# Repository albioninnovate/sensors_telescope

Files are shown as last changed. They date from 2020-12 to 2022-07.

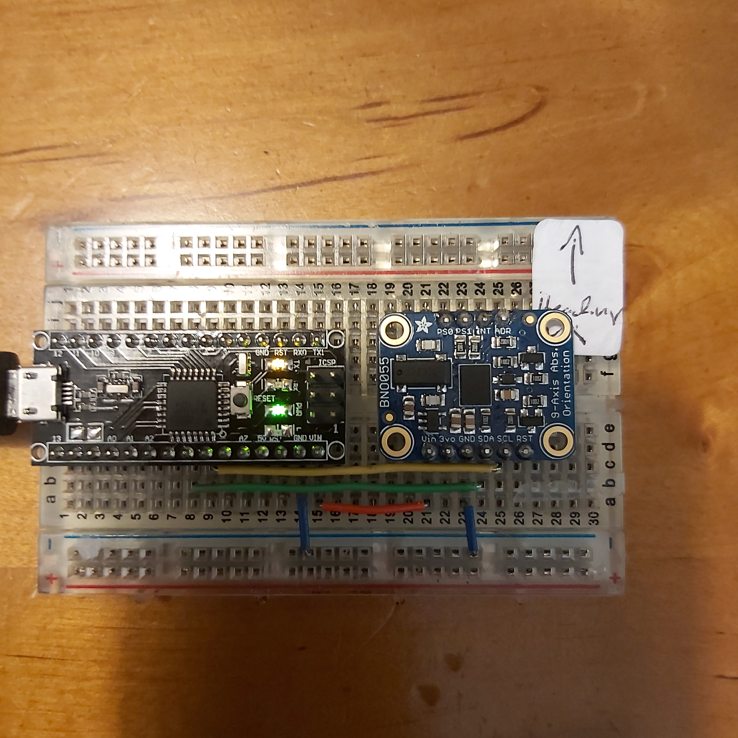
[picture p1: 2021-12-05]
arduino/images/20201223_222857.jpg

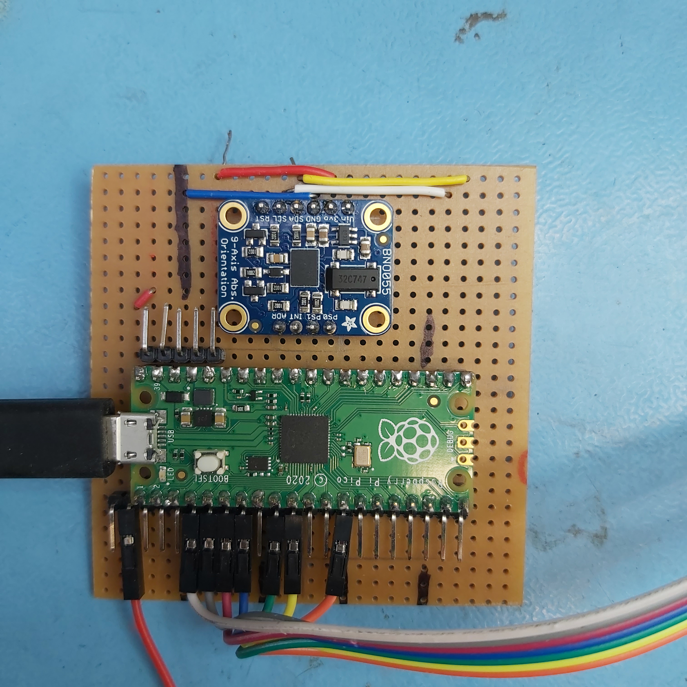
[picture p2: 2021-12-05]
Images/20210328_164021.jpg

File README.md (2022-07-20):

# Sensors_telescope
Sensor package for positioning telescope, to track targets, interfacing with astronomy software (Stellarium). 

## BNO055 Board layout and orientation:
         +----------+
         |         *| RST   PITCH  ROLL  HEADING
     ADR |*        *| SCL
     INT |*        *| SDA     ^            /->
     PS1 |*        *| GND     |            |
     PS0 |*        *| 3VO     Y    Z-->    \-X
         |         *| VIN
         +----------+

# Design

## Hardware configuration choice 

The initial strategy was to connect the BNO055 to a Raspberry Pi via I2C.  Although it was easy enough to get data from the sensor package the values were erratic.  Several approaches were taken too, speed up data collection, take larger samples followed by averaging and also to carry the data in quaternions and calculate the Euler angels in the last step. It seems the I2C connection is perhaps not fast enough to collect the useful measurements.

A second strategy it was much more successful. This was using an I2C connection via an Arduino and a USB connection between the Arduino and a Raspberry Pi.  The data return was very steady.   The demo Arduino scripts were more than sufficient to return the heading, pitch and yaw (azimuth, altitude and tilt) along with some data quality indicators. 

## Data choice 
The BNO055 outputs several types of direct measurements (Mag, Gyro, Acc, etc) and two sets of derived information, Euler Angles and Quaternions.  A quick review of literature suggests that Euler Angles can be problematic, and it is best to use quaternions in any data manipulations only converting to Euler angels in the last steps. 
This does not see to hold for the BNO055.  Initially data was erratic prompting a strategy of averaging the output.  The output is received in multi layer dictionary structures, so a utility was written to flatten the dictionary and average them (utils/flatten_dict.py).  Another utility was written to convert quaternions to Euler angels (utils/quaternion.py). 

The Euler angles output it from the sensor seem to be quite stable and correspond well with the orientation of the chip.  the decision was made to use the output from the chip directly ignoring the quaternions for now. It is worth investigating the processing done on the microprocessor of the BNO055 there appears to be some smoothing in the output data evidenced by its stability. 

When the Euler angles are sent Stellarium they must first be inverted by multiplying by -1 and then converting into radians 

## Python Choice 

Python => 3.8 is used in order to access asyncio functions.

An installation was created here:
```
/home/pi/Python-3.8.5
```

There are two installations of Python on this Raspberry Pi 3.5 is the standard which can be accessed by  $ python <>.py.  There is also an installation of Python 3.8 (home/pi/Python-3.8.5 which can be accessed with python38. <>.py.  The alias of this second installation is controlled in bashrc.
```
sudo nano /home/pi/.bashrc
```

the following line was added at the end of the file: 
```
alias python38="/home/pi/Python-3.8.5/python"
```

The reason for doing this was to access functionality in the asyncio package, specifically the. run method of that package. Running under early versions of python causes this error: 

AttributeError: module 'asyncio' has no attribute 'run'

### Installing packages 
Installing packages to this alternative python can be done via pip specifying  python38.
```
python38 -m pip install adafruit-circuitpython-bno055
```

## Information flow

It is anticipated that the information produced by the sensor will be used for more than one application for example; direct display at the telescope, feedback to the positioning system and sending orientation information to external programmes like Stellarium.  To accommodate this an architecture which allowed the sensor to continually produce data that could be requested by various clients.  

The system comprises a BNO055 connected by I2C to an Arduino sending data via a serial connexion to a Raspberry Pi running a simple server which is available over an IP network.   



# Telescope Capabilities

The goal of the project is that the pointing direction of the Optical Tube Assembly (OTA) is available to the user with only 5v power at the telescope. The user should be able to have "push to" functionally without any other computer or network connection.  This implies that simple calibrations are part of the system.   This latter capability is only practically possible with a some type of use interface, say buttons on the LCD screen.  

If more computing capability, and power is available, data recording, coordination with astronomy software (e.g. Stellarium), or motor drivers become a goal. 

# Ardunio setup 

ref: https://learn.adafruit.com/adafruit-bno055-absolute-orientation-sensor/arduino-code

an Arduino Mega was used for prototyping and in the future is a possibility for driving motors.  To connect the assembled BNO055 breakout to an Arduino

Pinouts:

| BNO055 | Arduino Mega | Arduino Nano |
| :--- | :---: | ---: |
|  SCL | 21  | A5 |
| SDA  | 20 | A4 |
| VIN  | 5v | VIN |
| GND  | GND | GND |

for mounting on the telescope the smaller form factor of a nano has advantages. 

See the Adafruit instructions for the necessary libraries.  The sketch is here arduino/bno055/bno055.ino.  Note the directory 'bno055' is needed by the Arduino IDE, do not remove it.

# PICO set up 

## Pinouts

## Software

### Circuitpython

#### Installation 

#### Requirements

#### Software
 bno055.py

 lcd_rgb.py

# LCD Screen

Adafruit RGB Negative 16x2 LCD+Keypad Kit for Raspberry Pi (ref: https://www.adafruit.com/product/1110

* pull up resistors needed, 5v logic 

Character LCD
https://circuitpython.readthedocs.io/projects/charlcd/en/latest/

# Server

In development and testing a Rpi 3 running a fresh installation of Buster was used.

Running the server has several requirements.

* Start on boot so that all that is required in the field is power on. 
* Be accessible via fixed IP or hostname from the laptop
* the host name needs to match in both the server and the client.  The host name should match the server, e.g. triscopepi.local or devpi.local.
* TODO add the host name to the configuration file so thi can be changed in just one place.
``` 
triscopepi.local
```
* Robustly find the serial port of the PICO/Arduino 

## Start on boot

Crontab is used to launch the server when the Rpi is powered. An updated version of Python3 was added to gain asyncio (https://docs.python.org/3.7/library/asyncio.html). 

ref: https://www.raspberrypi.org/documentation/linux/usage/cron.md

Edit Crontab on the Rpi by opening a terminal and executing the command: 
```
crontab -e
```

If asked select the nano editor.  In the file that opens, add this line.
```
@reboot sleep 30;/usr/bin/python3 /home/pi/code/sensors_triscope/rpi/server.py
```
A python version later than 3.7 be used so that asyncio is available.  A sleep of 30 seconds allows the Rpi to fully boot and establish network connections.  This has not be fully tested so other values, or elimination,  might also work

the sleep 30, allow time for the network connection and IP address to be established.  

There is an alternative approach for launching the server at startup, Systemd.  NOTE, the following approach has not always 
worked, while the cron approach has been reliable. 

---
see: 
    rpi/README_server.md
---
Setting server to run on RaspberryPi boot:
    
Create a Unit file 
```
sudo nano /lib/systemd/system/triscope_server.service
````

Add this text 
```
 [Unit]
 Description= Sensors Triscope Server
 After=multi-user.target

 [Service]
 Type=idle
 ExecStart=/usr/bin/python3 /home/pi/code/sensors_triscope/rpi/server.py

 [Install]
 WantedBy=multi-user.target
```

Set permission of the unit file to: 

```
sudo chmod 644 /lib/systemd/system/triscope_server.service
```

----

# client 
in the line:
  reader, writer = await asyncio.open_connection('triscopepi.local', 8888)

the host name can be used if that matches the IP address. In the case of two networks being active (Ethernet and WI-FI) the Rpi may have two addresses.  The connection can be forced over the direct link ether net byt switching off the WI-FI and making a call to the server via the host name.  After this is done the Wi-Fi can be switched back on with the host name remaining associated  with the ethernet connection   

# Stellarium Set up

ref https://stellarium.org/doc/head/remoteControlApi.html

Launch Stellarium Application 

Go to 	
1. Configuration Menu (F2)
2. Select the Plug-ins icon (top of dialogue box)
3. Select Remote Control plug-in (left of dialogue box)
4. Check box - launch at startup

Restart Stellarium Application to load plug-in

Return to the Remote Control plug-in

1. Click the Configure button
2. Check box: the Server enabled box 
   1. Returns: listening on 127.0.1.1
3. Confirm: Port number: 8096
4. Check box: Enable automatically at start up 
5. Save settings

# Real Time Clock 
ref: https://learn.adafruit.com/adafruit-pcf8523-real-time-clock/rtc-with-circuitpython

to run on PICO 

requirements: 

    adafruit_bus_device folder
    adafruit_register folder
    adafruit_pcf8523.mpy

to Set the time: 
``` 
if False:   # change to True if you want to write the time!
    #                     year, mon, date, hour, min, sec, wday, yday, isdst
    t = time.struct_time((2017,  10,   29,   15,  14,  15,    0,   -1,    -1))
    # you must set year, mon, date, hour, min, sec and weekday
    # yearday is not supported, isdst can be set but we don't do anything with it at this time

```

Change the False to True in the first line, and update the time.struct_time to have the current time starting from year to weekday. The last two entries can stay at -1

Note the part where the program says it is Setting time to:

Now you can go back and change the if True to if False and save, so you don't re-set the RTC again.

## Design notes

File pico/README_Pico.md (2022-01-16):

## PICO set up

The directory PICO_requirements contains all the files and lib requirements 
needed to run bno055.py and bno055_display.  Place it in the 
PICO directory ' CIRCUITPY '.   USe Mu to run and serial to display the 
output

# CircuitPython 

latest drivers can be found here:
https://github.com/adafruit/Adafruit_CircuitPython_Bundle/releases

https://github.com/adafruit/Adafruit_CircuitPython_Bundle/releases/tag/20220114

TODO  copy the active code and requirements folder from the PICO on the Triscope 

To reset PICO:
https://www.raspberrypi.com/documentation/microcontrollers/raspberry-pi-pico.html#resetting-flash-memory
https://datasheets.raspberrypi.com/soft/flash_nuke.uf2

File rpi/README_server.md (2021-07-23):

# Server

## Architecture choice 

TODO

## Supporting modules 

### ard_ser.py

TODO

## Sever set up

There are two approaches to launching the server at boot; systemd and crontab.

### crontab

```
crontab -e
```

Place the following text at the bottom of the file

```
@reboot sleep 30;/usr/bin/python3 /home/pi/code/sensors_triscope/rpi/server.py
```

----

### systemd

ref https://www.raspberrypi-spy.co.uk/2015/10/how-to-autorun-a-python-script-on-boot-using-systemd/

The intention is that the server.py module runs at boot of the RaspberryPi platform. This allows reset of the Raspberrypi-Arduino-BNO055 system to be reset with a power cycle of the Raspberrypi. The Arduino and sensor are powered by the Raspberrypi via the USB port.  

The server is at this location in the repository to allow ready maintenance: 
```
home/pi/code/sensors_telescope/raspberrypi/server.py
```

systemd is used to manage the startup process.  Systems is configured in a 'unit file'

``` 
 sudo nano /lib/systemd/system/server.service
 ```

this project uses the python3.7+ in order to access the asyncio features (TODO add reference to main README.md)

Add in the following text :
```
[Unit]
 Description=Sensors_telescope_server
 After=multi-user.target

 [Service]
 Type=idle
 ExecStart=/home/pi/Python-3.8.5/python /home/pi/code/sensors_triscope/rpi/server.py > /home/pi/code/sensors_triscope/rpi/server.log 2>&1

 [Install]
 WantedBy=multi-user.target
```

In order to store the script’s text output in a log file you can change the ExecStart line to :
```
ExecStart=/home/pi/Python-3.8.5/python home/pi/code/sensors_telescope/rpi/server.py > home/pi/code/sensors_telescope/rpi/server.log 2>&1

```

The permission on the unit file needs to be set to 644 :
```
sudo chmod 644 /lib/systemd/system/server.service
```

Configure systemd

Now the unit file has been defined we can tell systemd to start it during the boot sequence :

``` 
 sudo systemctl daemon-reload
 sudo systemctl enable server.service
 ```

Reboot the Pi and your custom service should run :

sudo reboot

The status of the server can be checked with:
 ```
 sudo systemctl status server.service
 
 sudo systemctl status /home/pi/Python-3.8.5/python home/pi/code/sensors_telescope/rpi/server.py 
 ```

### Troubleshooting 

sudo -H pip3 install serial -t /home/pi/Python-3.8.5

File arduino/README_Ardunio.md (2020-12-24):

ref: https://learn.adafruit.com/adafruit-bno055-absolute-orientation-sensor/arduino-code

## From AdaFruit
To connect the assembled BNO055 breakout to an Arduino Uno, follow the wiring diagram.

    Connect Vin (red wire) to the power supply, 3-5V is fine. Use the same voltage that the microcontroller logic is based off of. For most Arduinos, that is 5V
    Connect GND (black wire) to common power/data ground
    Connect the SCL (yellow wire) pin to the I2C clock SCL pin on your Arduino. On an UNO & '328 based Arduino, this is also known as A5, on a Mega it is also known as digital 21 and on a Leonardo/Micro, digital 3
    Connect the SDA (blue wire) pin to the I2C data SDA pin on your Arduino. On an UNO & '328 based Arduino, this is also known as A4, on a Mega it is also known as digital 20 and on a Leonardo/Micro, digital 2

## Arduino Nano
SCL - A5
SDA - A4
VIN - VIN
GND - GND

## Board layout:
         +----------+
         |         *| RST   PITCH  ROLL  HEADING
     ADR |*        *| SCL
     INT |*        *| SDA     ^            /->
     PS1 |*        *| GND     |            |
     PS0 |*        *| 3VO     Y    Z-->    \-X
         |         *| VIN
         +----------+

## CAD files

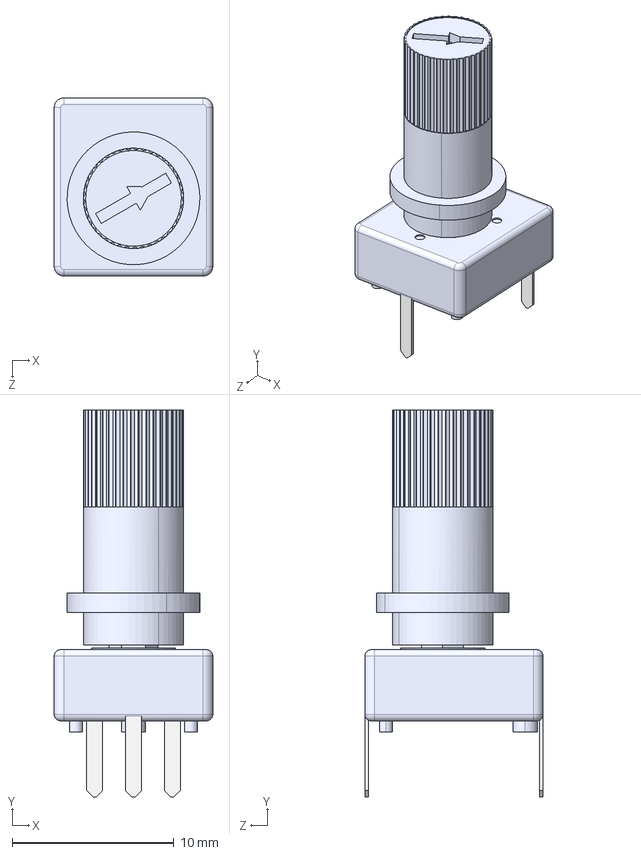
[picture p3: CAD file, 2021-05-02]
3d_model/Potentiometer_Square/PotSquareAssySTEP.STEP
9.80 x 23.9 x 11.0 mm
Pot_SquareBase
ShaftSocket
ShaftKnob

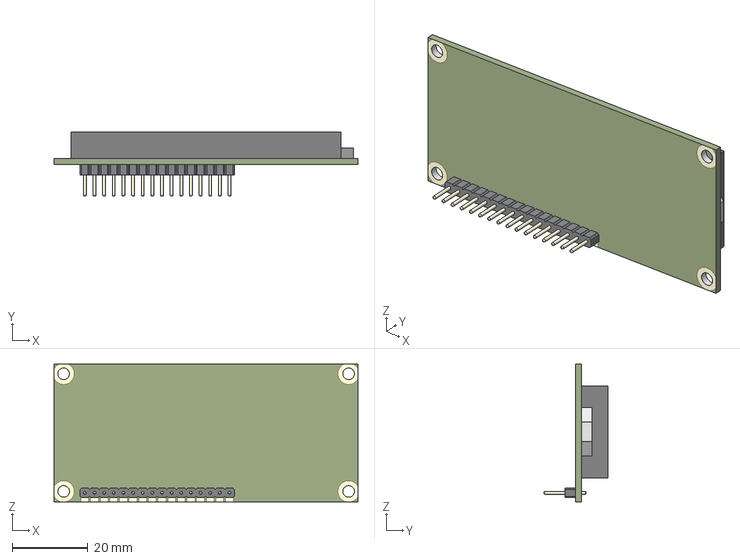
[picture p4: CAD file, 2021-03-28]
3d_model/1602a-lcd-module-1.snapshot.1/1602A - LCD w Header Pins.stp
80.1 x 17.0 x 36.3 mm
1602A - 16x2 LCD
16pin, Single Row, Male, Header, 0.1in pitch

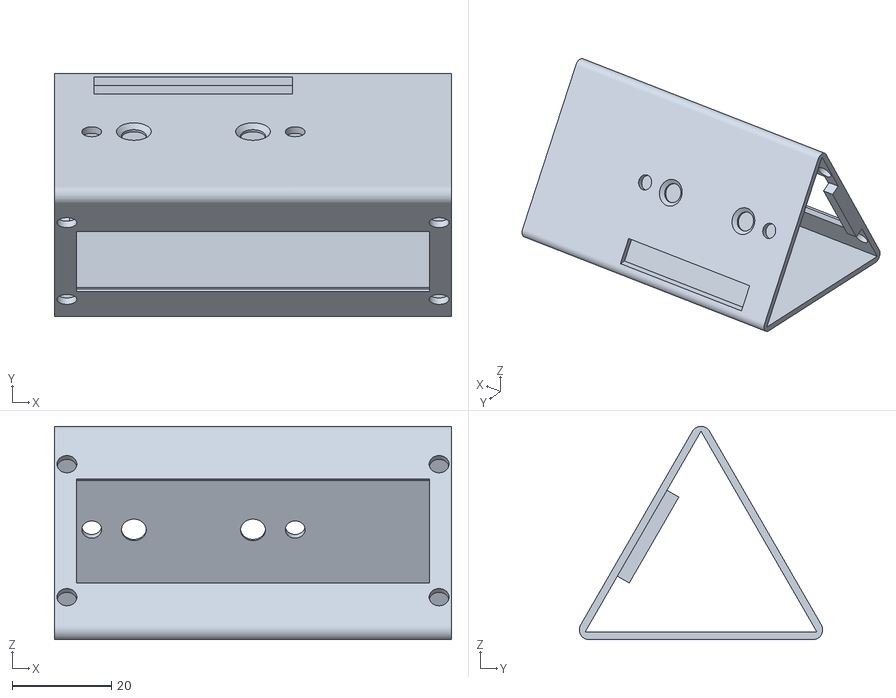
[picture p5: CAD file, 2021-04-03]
3d_model/LCD_case/LCD_case-Fusion007.stl
80.0 x 49.0 x 43.0

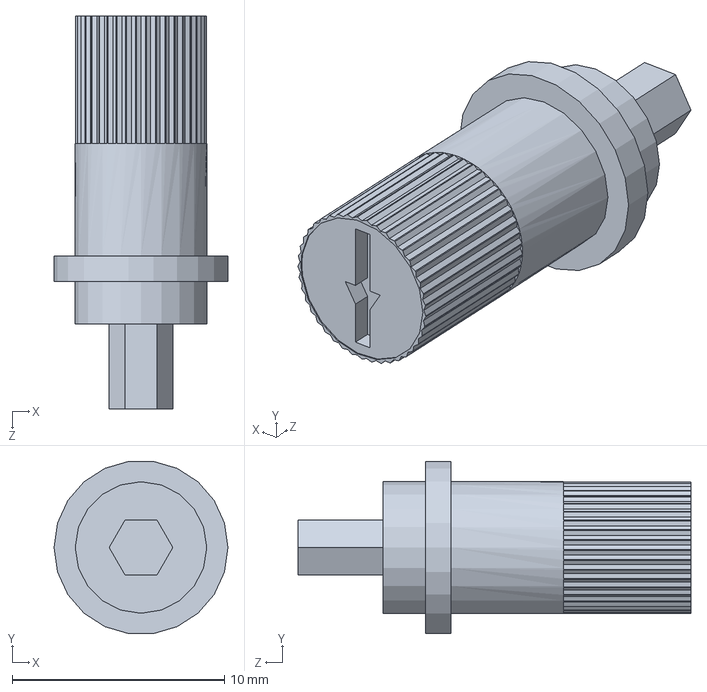
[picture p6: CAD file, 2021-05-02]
3d_model/Potentiometer_Square/ShaftKnob.SLDPRT
8.20 x 8.12 x 18.5 mm

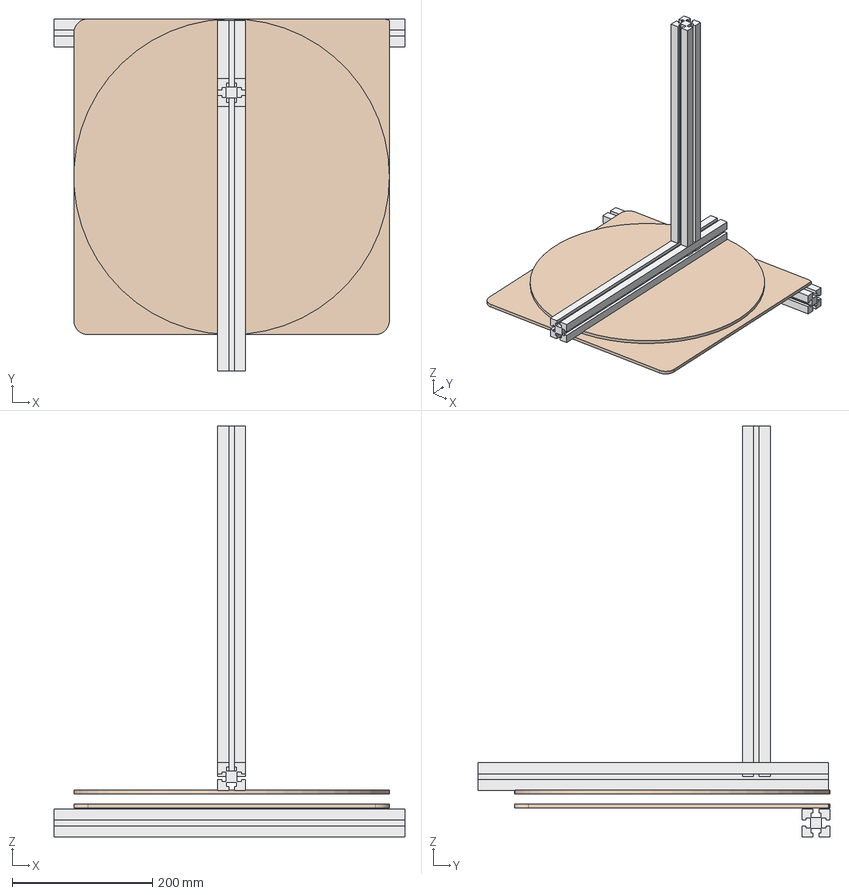
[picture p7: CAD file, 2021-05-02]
3d_model/Stand.FCStd
500.0 x 502.0 x 586.0 mm
Stand_Base
Stand_Strut
Stand_Strut_Base_001
Stand_Strut_Cross

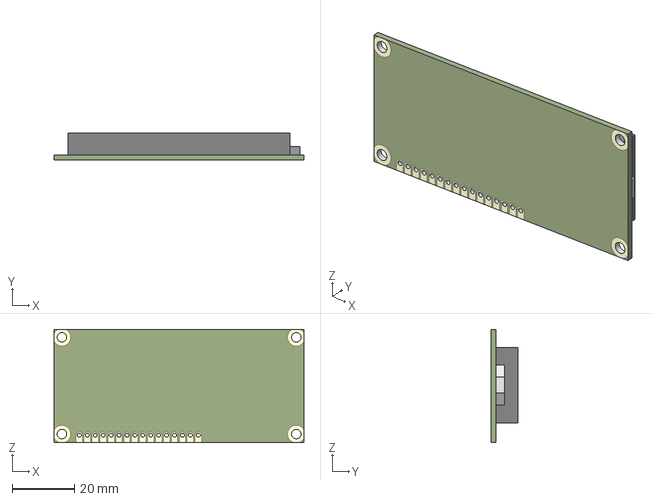
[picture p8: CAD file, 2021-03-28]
3d_model/1602a-lcd-module-1.snapshot.1/1602A - 16x2 LCD.stp
80.1 x 8.59 x 36.3 mm

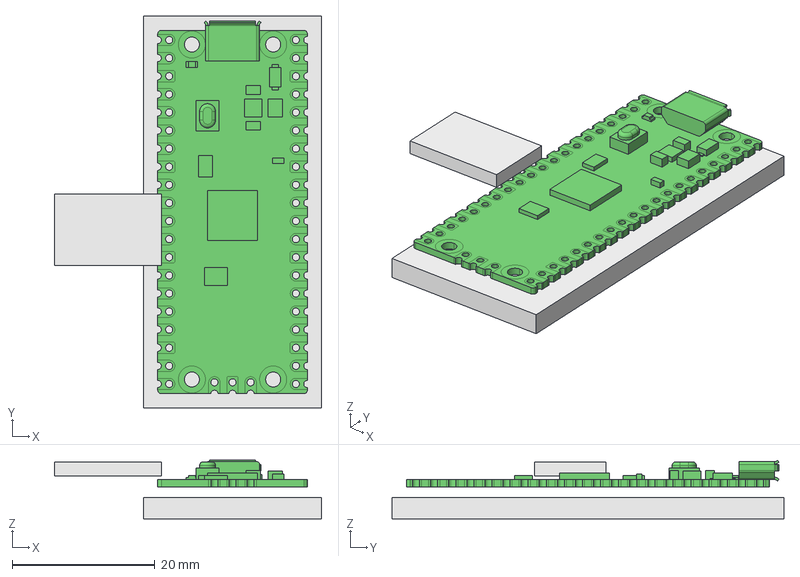
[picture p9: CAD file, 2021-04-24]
3d_model/pico-mount.FCStd
37.5 x 55.0 x 8.23 mm
pico-mount
PICO001

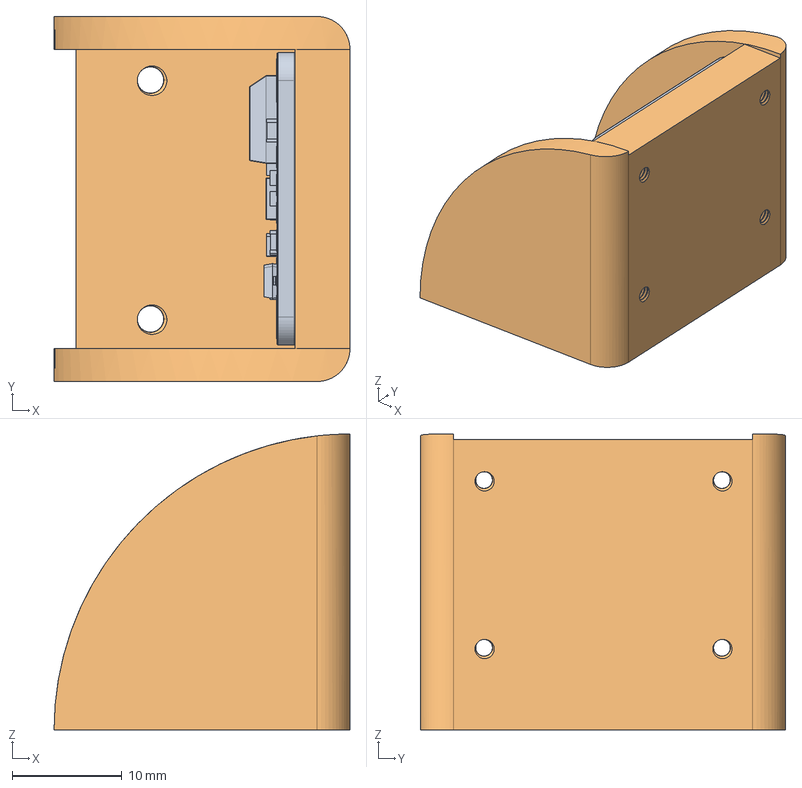
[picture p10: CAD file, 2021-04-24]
3d_model/bno055_mount.FCStd
27.0 x 33.3 x 27.0 mm
Adafruit_BNO055_AP214
BNO055-mount
BNO055-mount001

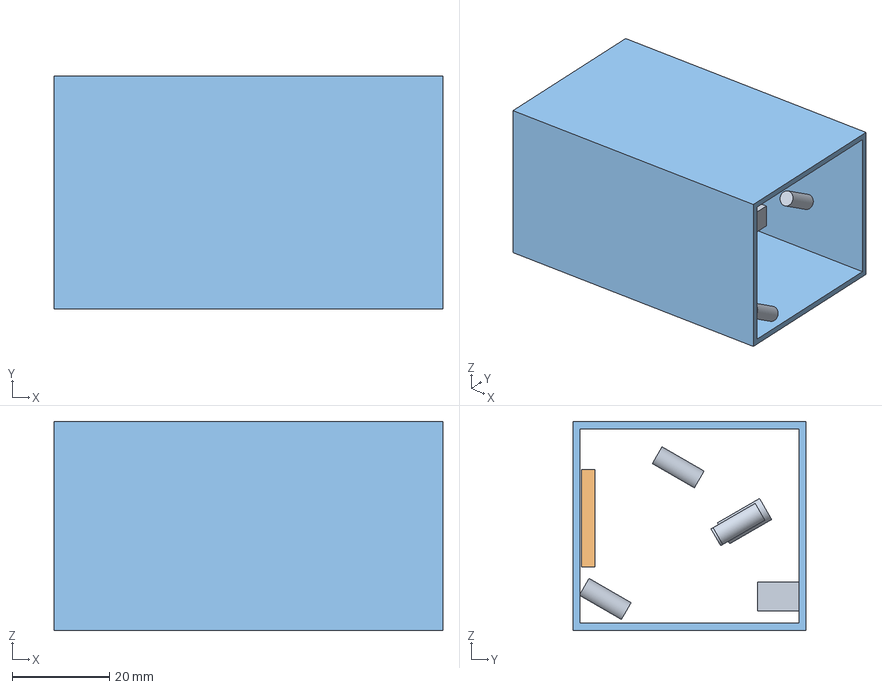
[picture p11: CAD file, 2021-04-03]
3d_model/LCD_case_sqr.FCStd
80.0 x 48.0 x 43.0 mm
LCD_case_tools
lcd_rest
Case

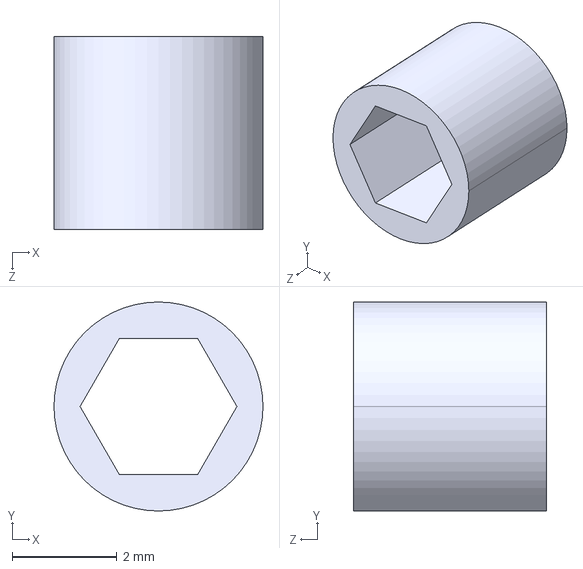
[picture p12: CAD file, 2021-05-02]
3d_model/Potentiometer_Square/ShaftSocketSTEP.STEP
4.00 x 4.00 x 3.70 mm

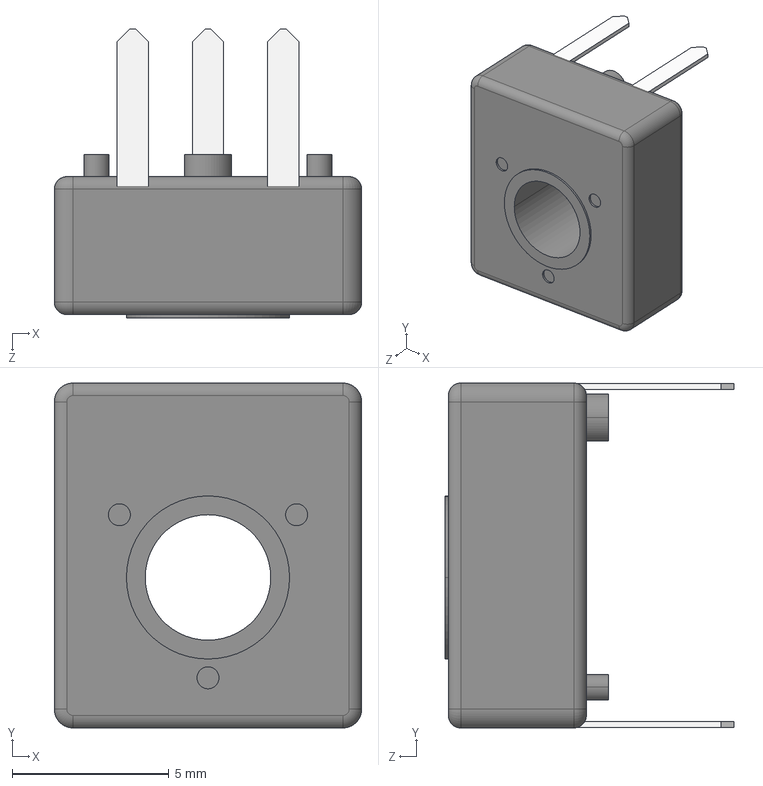
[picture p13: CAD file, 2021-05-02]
3d_model/Potentiometer_Square/Pot_SquareBaseSTEP.STEP
9.80 x 11.0 x 9.20 mm

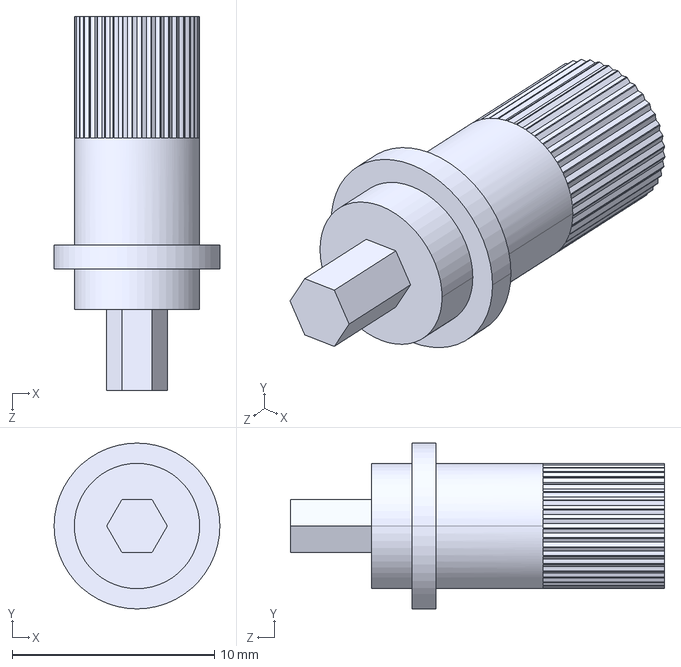
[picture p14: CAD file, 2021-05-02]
3d_model/Potentiometer_Square/ShaftKnobSTEP.STEP
8.20 x 8.20 x 18.5 mm

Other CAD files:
3d_model/Potentiometer_Square/PotSquareAssy.SLDASM
3d_model/LCD_case.FCStd
3d_model/Potentiometer_Square/ShaftSocket.SLDPRT
3d_model/Potentiometer_Square/Pot_SquareBase.SLDPRT

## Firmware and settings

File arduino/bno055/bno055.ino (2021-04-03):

#include <Wire.h>
#include <Adafruit_Sensor.h>
#include <Adafruit_BNO055.h>
#include <utility/imumaths.h>

/* This driver reads raw data from the BNO055

   Connections
   ===========
   Connect SCL to analog 5
   Connect SDA to analog 4
   Connect VDD to 3.3V DC
   Connect GROUND to common ground

   History
   =======
   2015/MAR/03  - First release (KTOWN)
*/

/* Set the delay between fresh samples */
/* #define BNO055_SAMPLERATE_DELAY_MS (100) */
#define BNO055_SAMPLERATE_DELAY_MS (1000)

// Check I2C device address and correct line below (by default address is 0x29 or 0x28)
//                                   id, address
Adafruit_BNO055 bno = Adafruit_BNO055(-1, 0x28);

/**************************************************************************/
/*
    Arduino setup function (automatically called at startup)
*/
/**************************************************************************/
void setup(void)
{
  Serial.begin(115200);
  /*
  Serial.println("Orientation Sensor Raw Data Test"); Serial.println("");*?

  /* Initialise the sensor */
  if(!bno.begin())
  {
    /* There was a problem detecting the BNO055 ... check your connections */
    Serial.print("Ooops, no BNO055 detected ... Check your wiring or I2C ADDR!");
    while(1);
  }

  delay(1000);

  /* Display the current temperature */
  /*int8_t temp = bno.getTemp();
  Serial.print("Current Temperature: ");
  Serial.print(temp);
  Serial.println(" C");
  Serial.println("");
  */

  bno.setExtCrystalUse(true);
/*
  Serial.println("Calibration status values: 0=uncalibrated, 3=fully calibrated");
*/
  
}

/**************************************************************************/
/*
    Arduino loop function, called once 'setup' is complete (your own code
    should go here)
*/
/**************************************************************************/
void loop(void)
{
  // Possible vector values can be:
  // - VECTOR_ACCELEROMETER - m/s^2
  // - VECTOR_MAGNETOMETER  - uT
  // - VECTOR_GYROSCOPE     - rad/s
  // - VECTOR_EULER         - degrees
  // - VECTOR_LINEARACCEL   - m/s^2
  // - VECTOR_GRAVITY       - m/s^2
  imu::Vector<3> euler = bno.getVector(Adafruit_BNO055::VECTOR_EULER);

  /* Display the floating point data */

  Serial.print("X: ");
  Serial.print(euler.x());
  Serial.print(" Y: ");
  Serial.print(euler.y());
  Serial.print(" Z: ");
  Serial.print(euler.z());
  Serial.print("\t\t");


  /*
  // Quaternion data
  */
  
  imu::Quaternion quat = bno.getQuat();
  Serial.print("qW: ");
  Serial.print(quat.w(), 4);
  Serial.print(" qX: ");
  Serial.print(quat.x(), 4);
  Serial.print(" qY: ");
  Serial.print(quat.y(), 4);
  Serial.print(" qZ: ");
  Serial.print(quat.z(), 4);
  Serial.print("\t\t");
 

  /* Display calibration status for each sensor. */
  uint8_t system, gyro, accel, mag = 0;
  bno.getCalibration(&system, &gyro, &accel, &mag);
  Serial.print("Sys=");
  Serial.print(system, DEC);
  Serial.print(" Gyro=");
  Serial.print(gyro, DEC);
  Serial.print(" Accel=");
  Serial.print(accel, DEC);
  Serial.print(" Mag=");
  Serial.println(mag, DEC);

  delay(BNO055_SAMPLERATE_DELAY_MS);
}

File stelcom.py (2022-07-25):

"""
    For modifications and text not covered by other licences:

    Original software Copyright (C) 2020 Ward Hills

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
"""


import math
import pprint
import requests
import client_pico_bno
import client


def get_status(propId=-2, actionId=-2, verbose=False):
    try:
        URL = "http://localhost:8090/api/main/status"

        PARAMS = {"propId": propId, "actionId": actionId}

        status = requests.get(url=URL, params=PARAMS)

        if verbose:
            print(URL)
            print(PARAMS)
            pprint.pprint(status.json())

        return status.json()

    except Exception:
        # print(e)
        print("Is Stellarium running with the remote control plugin?")


"""
ref https://stellarium.org/doc/head/remoteControlApi.html

Launch Stellarium Application 
go to 
	1. Configuration Menu (F2)
	2. plug-in
Select Remote Control plug-in
	Options - launch at startup

Restart Stellarium Application to load plug-in

Return to the Remote Control plug-in
		Click the Configure button 
		Check the Server enabled box
				Returns: listening on 127.0.1.1
		Confirm: Port number: 8096
		Check the Enable automatically at start up box
		Save settings 
"""

def send_altaz(_az=0, _alt=0):
    """

    :_az   In radians
    :_alt  In radians
    :return:
    """

    # api-endpoint
    URL = "http://localhost:8090/api/main/view"

    # az and alt must be given in radians.
    # -1 to correct for differences in the coor system

    # defining a params dict for the
    # parameters to be sent to the API
    PARAMS = {"az": _az, "alt": _alt}

    # sending get request and saving the response as response object
    r = requests.post(url=URL, params=PARAMS)
    return r


def send_fov(fov=20):
    URL = "http://localhost:8090/api/main/fov"
    r = requests.post(url=URL, params={"fov": fov})
    return r


if __name__ == '__main__':
    propId = 1
    actionId = 1
    s = get_status(propId, actionId, verbose=False)
    # pprint.pprint(s)

    # print('J Day :', s['time']['jday'])

    while True:
       # received = client.main()
        received = client_pico_bno.main()
        # print('Euler angles : ', received['Euler angle'])

        # az = float(received['X'])
        # alt = float(received['Z'])

        az = float(received[0])
    #    alt = float(received[2])

        # if sensor is 'reverse' mounted
        alt = float(received[2])  * -1

        #az_rad = - math.radians(az) - math.pi
#        az_rad = - math.radians(az)
        az_rad = - (math.radians(az) ) -math.pi
        alt_rad = math.radians(alt)

       # print("Az/Alt : ", az_rad, ' / ', alt_rad)

        x = 0
        while x <= 1:
            send_altaz(az_rad, alt_rad)
#            send_fov(40)
            x += 1

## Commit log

2020-12-09 information past verified, Euler and Orientation value are returing zeros from the sensor.
2020-12-09 values being transmitted from sensor to Stellarium; very noisy data
2020-12-09 working end to end, next steps to add averaging to reduce jitter and real time plotting to see if there is a pattern to the jitter
    [bno055.py, client.py, server.py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]
2020-12-12 plotting function working for single quantitiy. The data rate is slow. Next steps fetch only some data and average it eariler in data flow
2020-12-12 update server and bno055 removing print statements. Logging and configparser not working completely
    [bno055.py, client.py, server.py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]
2020-12-19 'timestamped sample og multiple IMU data sets being pasted to the client. Next step is to average the samples and pass to the animate module '
2020-12-19 bno055 passing mulitiple timestamped imu data sets
2020-12-21 added arduino HW, working, needs calibration and opto.
2020-12-21 modified client, animate to work with Arduino HW tested on Stele
2020-12-22 documentation and cleanup after refactoring to Arduino strategy. Averaging strategy abandoned.
2020-12-22 added quaternion data to replace Euler angels
    [animate.py, arduino_serial.py, client.py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]
2020-12-22 removed print line from Ardunio scrip and placed in directory
2020-12-24 updates to logging on Rpi modules. Performed a long term test; data goes to all 0's after ca 4000 readings with no movement. appears not recoverable with motion, arduino or software resets.
    [animate.py, ard_ser.py, client.py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]
2021-02-06 added pico code, working
2021-03-12 mod ard_srv.py to PICO
2021-03-19 created LCD Case
    [1602A - 16x2 LCD.stp, 1602A - LCD w Header Pins.stp, LCD_case.FCStd]
2021-03-27 added trim pots to LCD screen holder
    [LCD_case.FCStd, LCD_case.stl]
2021-03-28 created PICO requirements Dir. tested on new sensors mount board
2021-04-03 client code working end to end.
    [LCD_case.FCStd, LCD_case.stl]
2021-04-04 added bno055 muount
    [bno055_mount.FCStd]
2021-04-06 added pico mount updated bno055 mount
    [bno055_mount.FCStd, pico-mount.FCStd]
2021-04-08 sensor mount changes
    [pico-mount.FCStd]
2021-04-27 updated PICO req and tested after clean up merge
2021-04-27 tested after clean up merge + added calibration planning
2021-05-02 upate 3D Models and papers
    [PotSquareAssy.SLDASM, PotSquareAssySTEP.STEP, Pot_SquareBase.SLDPRT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]
2021-05-03 update PICO requirements
2021-05-14 added calibration true values genenerator
2021-05-17 added calibration tests prep
2021-07-23 Placed sensor on the end of the OTA and reversed it )rotated on Z 180 deg. Tested to 2-3% pointing error uncalibrated.
    [animate.py, animate_geo.py, animate_polar.py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]
2022-01-15 update circuit python
2022-01-19 updated Circuitpython and pico code
2022-07-20 Refactored to svr on PICO with BNO055. Working through to animate_polar.py
2022-07-30 addeed AP's IP address. Teste from laptop with it logedin to the AP running on the pico server

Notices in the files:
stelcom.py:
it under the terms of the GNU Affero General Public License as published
